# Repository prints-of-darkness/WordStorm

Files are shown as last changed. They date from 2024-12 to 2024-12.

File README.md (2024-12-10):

# Thermal Typewriter Project

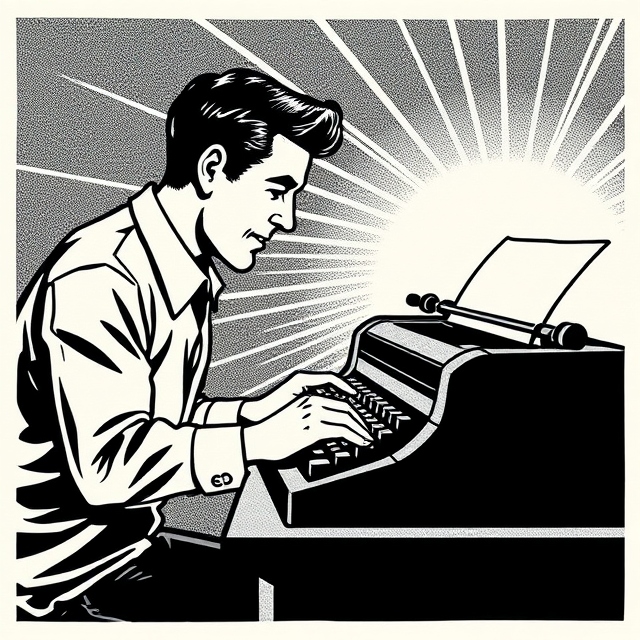
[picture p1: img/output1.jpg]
typewriter


 # Online BOM
 
 [BOM - WordStorm Cable Assy](https://www.digikey.com/en/mylists/list/2O8VW37YGK)
 
 [BOM - WordStorm R1.0](https://www.digikey.com/en/mylists/list/FTYAIGX1OS)
 
 [BOM - WordStorm Button](https://www.digikey.com/en/mylists/list/06NHDMXKI4)
 
 [BOM - WordStorm Debugger](https://www.digikey.com/en/mylists/list/TRGR0LOKP3)
 
 # Project Links

[Case](https://github.com/prints-of-darkness/WordStorm-Case)

[Display Module](https://github.com/prints-of-darkness/WordStorm-Display)

[Code](https://github.com/prints-of-darkness/WordStorm-Code)

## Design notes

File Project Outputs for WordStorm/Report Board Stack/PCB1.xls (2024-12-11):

Board Stack Report
Stack Up |  | Layer Stack
Layer | Board Layer Stack | Name | Material | Thickness | Constant
1 |  | Top Overlay |  | 0mil
2 |  | Top Solder | Solder Resist | 0.5mil | 3.8
3 |  | Top Layer |  | 1.378mil
4 |  | Dielectric 1 | 2313 | 3.937mil | 4.05
5 |  | Mid Layer 1 |  | 0.689mil
6 |  | Core | FR-4 | 49.803mil | 4.5
7 |  | Mid Layer 2 |  | 0.689mil
8 |  | Dielectric 2 | 2313 | 3.937mil | 4.05
9 |  | Bottom Layer |  | 1.378mil
10 |  | Bottom Solder | Solder Resist | 0.5mil | 3.8
11 |  | Bottom Overlay |  | 0mil
 | Height : 62.811mil

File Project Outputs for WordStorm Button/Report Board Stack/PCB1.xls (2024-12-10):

Board Stack Report
Stack Up |  | Layer Stack
Layer | Board Layer Stack | Name | Material | Thickness | Constant
1 |  | Top Overlay |  | 0mil
2 |  | Top Solder | Solder Resist | 0.5mil | 3.8
3 |  | Top Layer |  | 1.378mil
4 |  | Dielectric | FR-4 | 59.055mil | 4.5
5 |  | Bottom Layer |  | 1.378mil
6 |  | Bottom Solder | Solder Resist | 0.5mil | 3.8
7 |  | Bottom Overlay |  | 0mil
 | Height : 62.811mil

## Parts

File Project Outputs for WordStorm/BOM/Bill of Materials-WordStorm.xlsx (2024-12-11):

Line # | Name | Description | Designator | Quantity
 | CEM-1203(42) | Buzzers Transducer, Externally Driven Magnetic 3.5 V 35mA 2.048kHz 85dB @ 3.5V, 10cm Through Hole PC Pins | BUZZ1 | 1
 | GRM188R72A104MA35J | 0.1 µF ±20% 100V Ceramic Capacitor X7R 0603 (1608 Metric) | C1, C4, C7, C9, C16, C17, C18, C19, C20, C36, C37, C38, C39, C40, C41, C43, C45, C48, C49, C50, C51, C52, C53 | 23
 | C2012X5R1V226M125AC | CAP CER 22UF 35V X5R 0805 | C2, C5, C6, C8, C10, C11 | 6
 | GRM188R6YA106MA73D | 10 µF ±20% 35V Ceramic Capacitor X5R 0603 (1608 Metric) | C3, C13 | 2
 | GRM1885C2A471JA01D | 470 pF ±5% 100V Ceramic Capacitor C0G, NP0 0603 (1608 Metric) | C12 | 1
 | GRM188R6YA475KE15D | 4.7 µF ±10% 35V Ceramic Capacitor X5R 0603 (1608 Metric) | C14 | 1
 | GRM188R72A223KAC4D | 0.022 µF ±10% 100V Ceramic Capacitor X7R 0603 (1608 Metric) | C15, C31 | 2
 | EEE-FTH101XAP | CAP ALUM 100UF 20% 50V SMD | C21, C32 | 2
 | GRM188R72A103KA01D | 0.01 µF ±10% 100V Ceramic Capacitor X7R 0603 (1608 Metric) | C28, C29, C33, C34 | 4
 | GRM188R71H224KAC4D | 0.22 µF ±10% 50V Ceramic Capacitor X7R 0603 (1608 Metric) | C30 | 1
 | GRM188R7YA474KE05D | 0.47 µF ±10% 35V Ceramic Capacitor X7R 0603 (1608 Metric) | C35 | 1
 | GRM188D71H105KE01J | 1 µF ±10% 50V Ceramic Capacitor X7T 0603 (1608 Metric) | C42, C44 | 2
 | GRM188R61E225KA12J | 2.2 µF ±10% 25V Ceramic Capacitor X5R 0603 (1608 Metric) | C46, C47 | 2
 | ESD9X3.3ST5G | 10.4V Clamp 9.8A (8/20µs) Ipp Tvs Diode Surface Mount SOD-923 | D1, D2 | 2
 | FDLL4148 | Diode 100 V 200mA Surface Mount SOD-80 | D3 | 1
 | 3413.0326.22 | 7 A 32 V AC 63 V DC Fuse Board Mount (Cartridge Style Excluded) Surface Mount 1206 (3216 Metric) | F1 | 1
 | MPZ1608S221ATA00 | 220 Ohms @ 100 MHz 1 Power Line Ferrite Bead 0603 (1608 Metric) 2.2A 50mOhm | FB1 | 1
 | 54-00128 | Power Barrel Connector Jack 2.50mm ID (0.098"), 5.50mm OD (0.217") Through Hole, Right Angle | J1 | 1
 | 0530470210 | Connector Header Through Hole 2 position 0.049" (1.25mm) | J2 | 1
 | 10033527-N3112MLF | USB - mini AB USB 2.0 Receptacle Connector 5 Position Surface Mount, Right Angle | J3 | 1
 | 292303-1 | USB-A (USB TYPE-A) USB 2.0 Receptacle Connector 4 Position Through Hole, Right Angle | J4 | 1
 | B34B-PHDSS | Connector Header Through Hole 34 position 0.079" (2.00mm) | J5 | 1
 | 0530470410 | Connector Header Through Hole 4 position 0.049" (1.25mm) | J6 | 1
 | SFV16R-1STBE1HLF | 16 Position FFC, FPC Connector Contacts, Bottom 0.020" (0.50mm) Surface Mount, Right Angle | J7 | 1
 | 1255AY-3R9N=P3 | 3.9 µH Shielded Drum Core, Wirewound Inductor 4.2 A 22mOhm Nonstandard | L1 | 1
 | 744314650 | 6.5 µH Shielded Wirewound Inductor 6 A 21.5mOhm Nonstandard | L2 | 1
 | SISS65DN-T1-GE3 | P-Channel 30 V 25.9A (Ta), 94A (Tc) 5.1W (Ta), 65.8W (Tc) Surface Mount PowerPAK® 1212-8S | Q1 | 1
 | MMBT2222A-7-F | Bipolar (BJT) Transistor NPN 40 V 600 mA 300MHz 310 mW Surface Mount SOT-23-3 | Q2, Q3 | 2
 | RMCF0603FG10K0 | 10 kOhms ±1% 0.1W, 1/10W Chip Resistor 0603 (1608 Metric) Automotive AEC-Q200 Thick Film | R1, R8, R11, R12, R15, R17, R22, R23, R24, R25, R26, R27, R28, R29, R30, R50, R52, R56 | 18
 | RMCF0603FG20K0 | 20 kOhms ±1% 0.1W, 1/10W Chip Resistor 0603 (1608 Metric) Automotive AEC-Q200 Thick Film | R2, R7 | 2
 | RMCF0603FT180R | 180 Ohms ±1% 0.1W, 1/10W Chip Resistor 0603 (1608 Metric) Automotive AEC-Q200 Thick Film | R3, R48 | 2
 | RMCF0603FG100K | 100 kOhms ±1% 0.1W, 1/10W Chip Resistor 0603 (1608 Metric) Automotive AEC-Q200 Thick Film | R4, R5, R6, R14, R16, R31, R33, R37, R49 | 9
 | RMCF0603FT360K | 360 kOhms ±1% 0.1W, 1/10W Chip Resistor 0603 (1608 Metric) Automotive AEC-Q200 Thick Film | R9 | 1
 | RMCF0603FT40K2 | 40.2 kOhms ±1% 0.1W, 1/10W Chip Resistor 0603 (1608 Metric) Automotive AEC-Q200 Thick Film | R10 | 1
 | RMCF0603FG1K00 | 1 kOhms ±1% 0.1W, 1/10W Chip Resistor 0603 (1608 Metric) Automotive AEC-Q200 Thick Film | R13, R19 | 2
 | YC164-JR-07100RL | 100 Ohm ±5% 62.5mW Power Per Element Isolated 4 Resistor Network/Array ±200ppm/°C 1206 (3216 Metric), Convex, Long Side Terminals | R18, R20, R21, R53, R54, R55 | 6
 | RMCF0603FG15K0 | 15 kOhms ±1% 0.1W, 1/10W Chip Resistor 0603 (1608 Metric) Automotive AEC-Q200 Thick Film | R32, R40, R42, R44, R46 | 5
 | RMCF0603FT48K7 | 48.7 kOhms ±1% 0.1W, 1/10W Chip Resistor 0603 (1608 Metric) Automotive AEC-Q200 Thick Film | R34 | 1
 | RMCF0603FT80K6 | 80.6 kOhms ±1% 0.1W, 1/10W Chip Resistor 0603 (1608 Metric) Automotive AEC-Q200 Thick Film | R35 | 1
 | RMCF0603FG16K0 | 16 kOhms ±1% 0.1W, 1/10W Chip Resistor 0603 (1608 Metric) Automotive AEC-Q200 Thick Film | R36 | 1
 | RMCF0603FT63K4 | 63.4 kOhms ±1% 0.1W, 1/10W Chip Resistor 0603 (1608 Metric) Automotive AEC-Q200 Thick Film | R38 | 1
 | RMCF0603FG39K0 | 39 kOhms ±1% 0.1W, 1/10W Chip Resistor 0603 (1608 Metric) Automotive AEC-Q200 Thick Film | R39 | 1
 | RMCF0603FG100R | 100 Ohms ±1% 0.1W, 1/10W Chip Resistor 0603 (1608 Metric) Automotive AEC-Q200 Thick Film | R41, R45 | 2
 | RMCF0603FG24K0 | 24 kOhms ±1% 0.1W, 1/10W Chip Resistor 0603 (1608 Metric) Automotive AEC-Q200 Thick Film | R43, R47 | 2
 | RMCF0603ZT0R00 | 0 Ohms Jumper Chip Resistor 0603 (1608 Metric) Automotive AEC-Q200 Thick Film | R51 | 1
 | 1040310811 | 10 (8 + 2) Position Card Connector Secure Digital - microSD™ Surface Mount, Right Angle Gold | SD1 | 1
 | AP63203WU-7 | Buck Switching Regulator IC Positive Fixed 3.3V 1 Output 2A SOT-23-6 Thin, TSOT-23-6 | U1 | 1
 | TPS7B6933QDCYRQ1 | Linear Voltage Regulator IC Positive Fixed 1 Output 150mA SOT-223-4 | U2 | 1
 | MP2338GTL-Z | Buck Switching Regulator IC Positive Adjustable 0.5V 1 Output 3A SOT-583 | U3 | 1
 | ATTINY85-20PU | AVR AVR® ATtiny, Functional Safety (FuSa) Microcontroller IC 8-Bit 20MHz 8KB (4K x 16) FLASH 8-PDIP | U4 | 1
 | STMPS2141STR | Power Switch/Driver 1:1 N-Channel 500mA SOT-23-5 | U5 | 1
 | TS3USB221ARSER | USB Switch IC 2 Channel 10-UQFN (2.0x1.5) | U6 | 1
 | SN74LVC2G34DBVR | Buffer, Non-Inverting 2 Element 1 Bit per Element Push-Pull Output SOT-23-6 | U7 | 1
 | SN74LVC541APWR | Buffer, Non-Inverting 1 Element 8 Bit per Element 3-State Output 20-TSSOP | U8 | 1
 | DRV8426RGER | Bipolar Motor Driver Power MOSFET Step/Direction 24-VQFN (4x4) | U9 | 1
 | MCP6561T-E/LT | Comparator General Purpose CMOS, Push-Pull, Rail-to-Rail, TTL SC-70-5 | U10, U11, U12, U13 | 4
 | W25Q64JVSSIQ | FLASH - NOR Memory IC 64Mbit SPI - Quad I/O 133 MHz 8-SOIC | U14 | 1
 | STM32H743VIT6 | ARM® Cortex®-M7 STM32H7 Microcontroller IC 32-Bit Single-Core 480MHz 2MB (2M x 8) FLASH 100-LQFP (14x14) | U15 | 1
 | APX809S-31SA-7 | Supervisor Push-Pull, Totem Pole 1 Channel SOT-23-3 | U16 | 1
 | CSTNE8M00G550000R0 | 8 MHz Ceramic Resonator Built in Capacitor 33 pF ±0.2% 40 Ohms -40°C ~ 85°C Surface Mount | X1 | 1

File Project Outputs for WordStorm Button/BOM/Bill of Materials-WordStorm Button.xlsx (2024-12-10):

Name | Description | Designator | Quantity
0530470210 | Connector Header Through Hole 2 position 0.049" (1.25mm) | J1 | 1
TS02-66-150-BK-100-LCR-D | Tactile Switch SPST-NO Top Actuated Through Hole | S1 | 1

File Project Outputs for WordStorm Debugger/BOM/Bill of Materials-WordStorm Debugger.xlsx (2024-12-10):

Name | Description | Designator | Quantity
SFH11-PBPC-D10-ST-BK | 20 Position Header Connector 0.100" (2.54mm) Through Hole Gold | J1 | 1
0530470410 | Connector Header Through Hole 4 position 0.049" (1.25mm) | J2 | 1

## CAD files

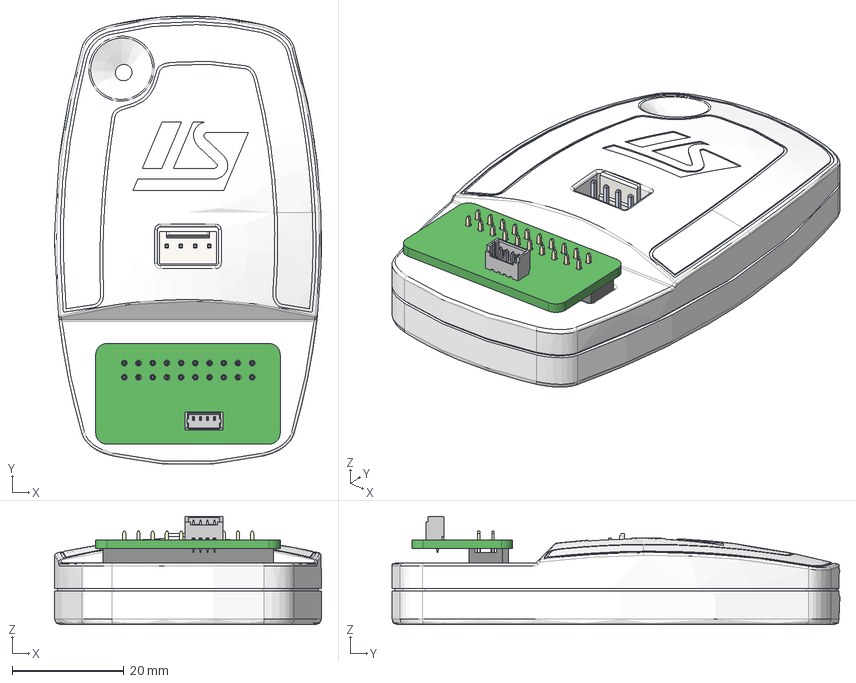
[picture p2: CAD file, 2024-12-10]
Debugger_Step/stlink_v2.step
47.7 x 80.1 x 19.4 mm
SFH11-xC-Dx-ST-BK body_10
pin^SFH11-xC-Dx-ST-BK Ass x 20
PinHeader_2x10_P254mm_Vertical
USB_Mini-B_Lumberg_2486_01_Horizontal
WF_(DS1070_CONNFLY)

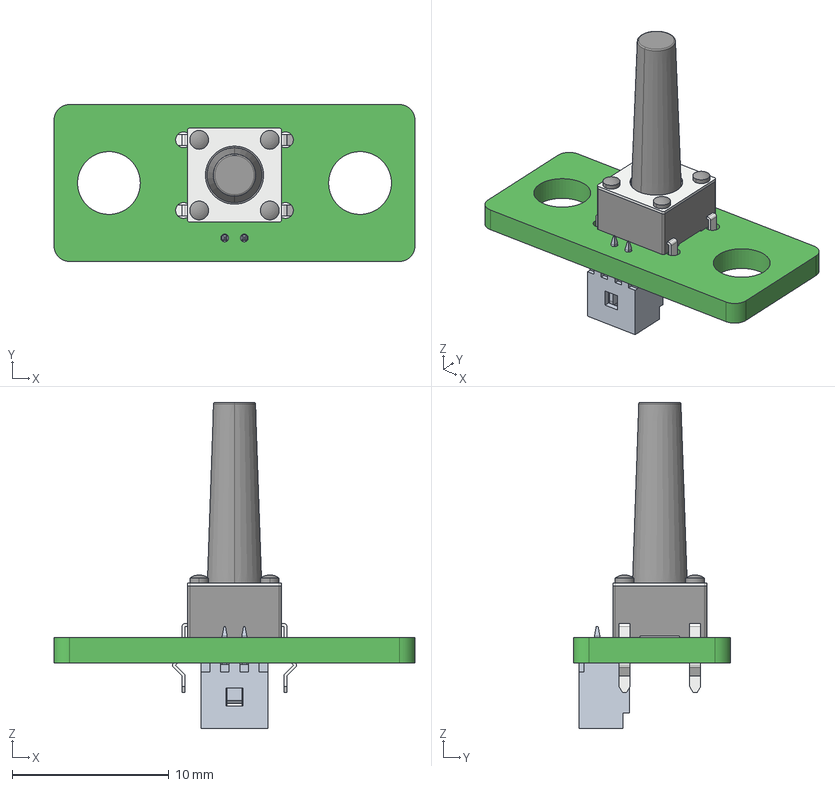
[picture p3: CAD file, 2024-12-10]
Project Outputs for WordStorm Button/ExportSTEP/PCB1.step
23.0 x 10.0 x 20.8 mm
Same_Sky_TS02-66-150-BK-100-LCR-D

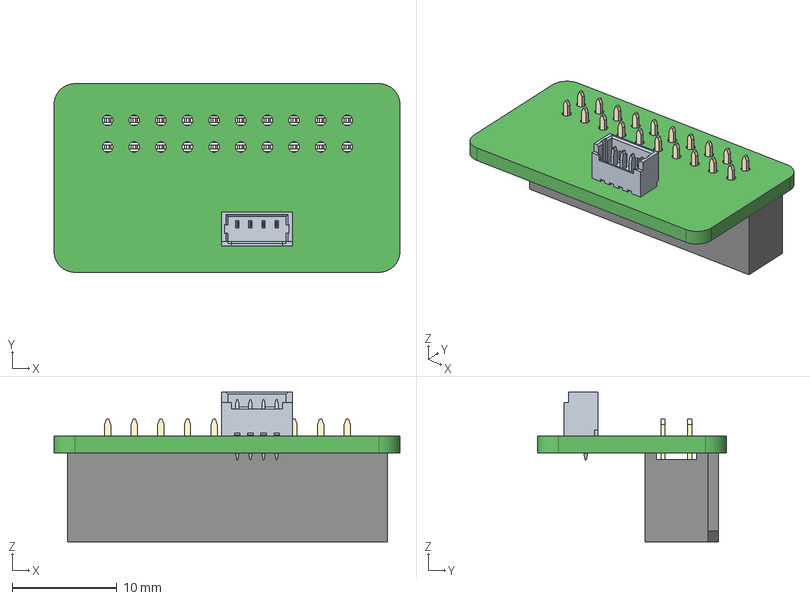
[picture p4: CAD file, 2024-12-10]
Project Outputs for WordStorm Debugger/ExportSTEP/PCB1.step
33.0 x 18.0 x 14.3 mm
SFH11-xC-Dx-ST-BK body_10
pin^SFH11-xC-Dx-ST-BK Ass x 20

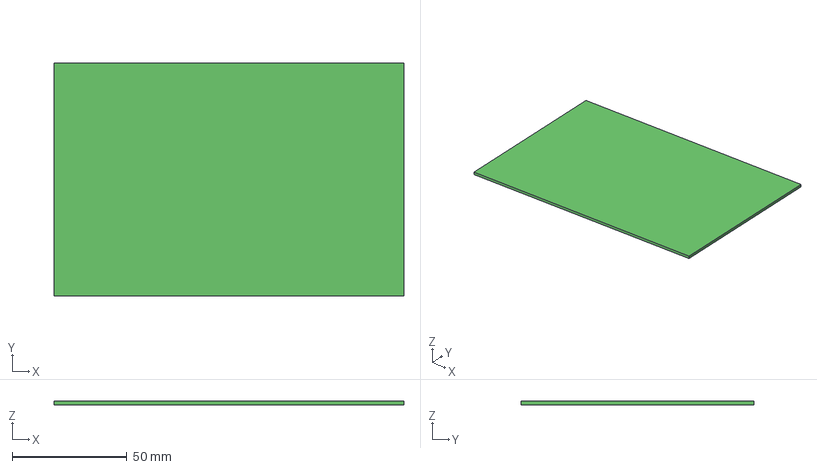
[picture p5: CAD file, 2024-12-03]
Project Outputs for WordStorm/ExportSTEP/PCB1.step
152.4 x 101.6 x 1.60 mm

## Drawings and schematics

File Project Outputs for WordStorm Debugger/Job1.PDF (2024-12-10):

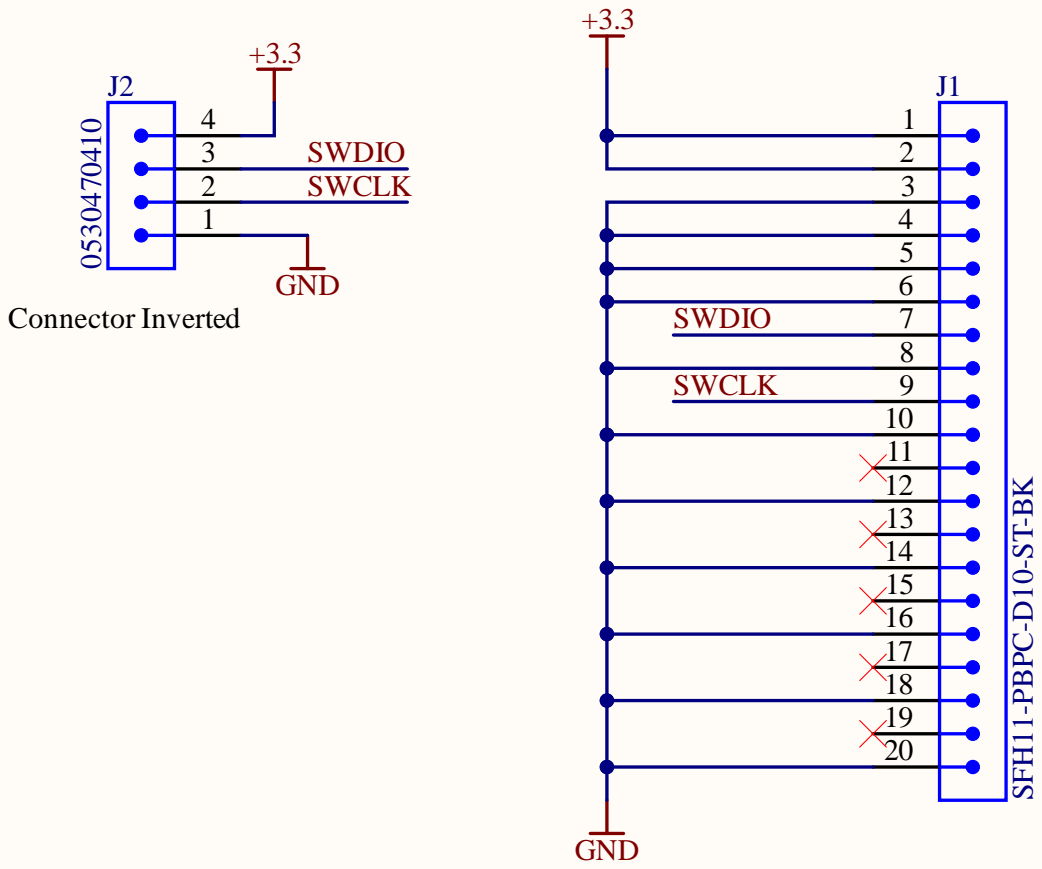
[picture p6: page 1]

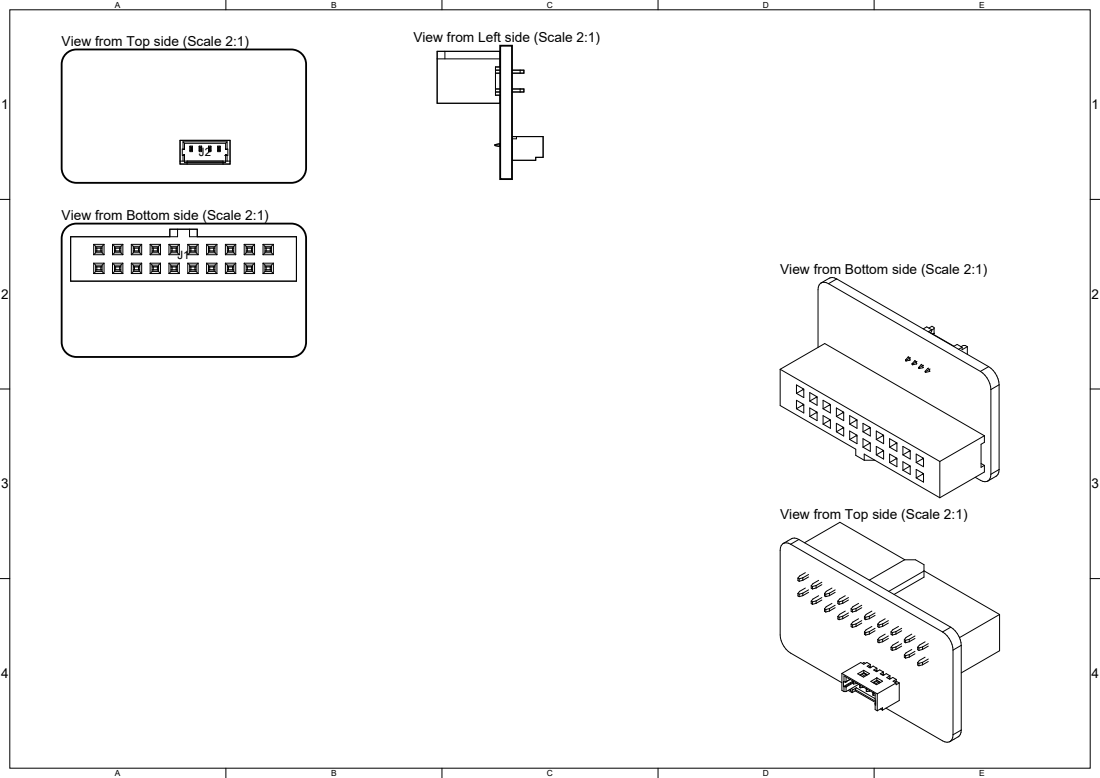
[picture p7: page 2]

View from Top side (Scale 2:1)

View from Left side (Scale 2:1)

View from Bottom side (Scale 2:1)

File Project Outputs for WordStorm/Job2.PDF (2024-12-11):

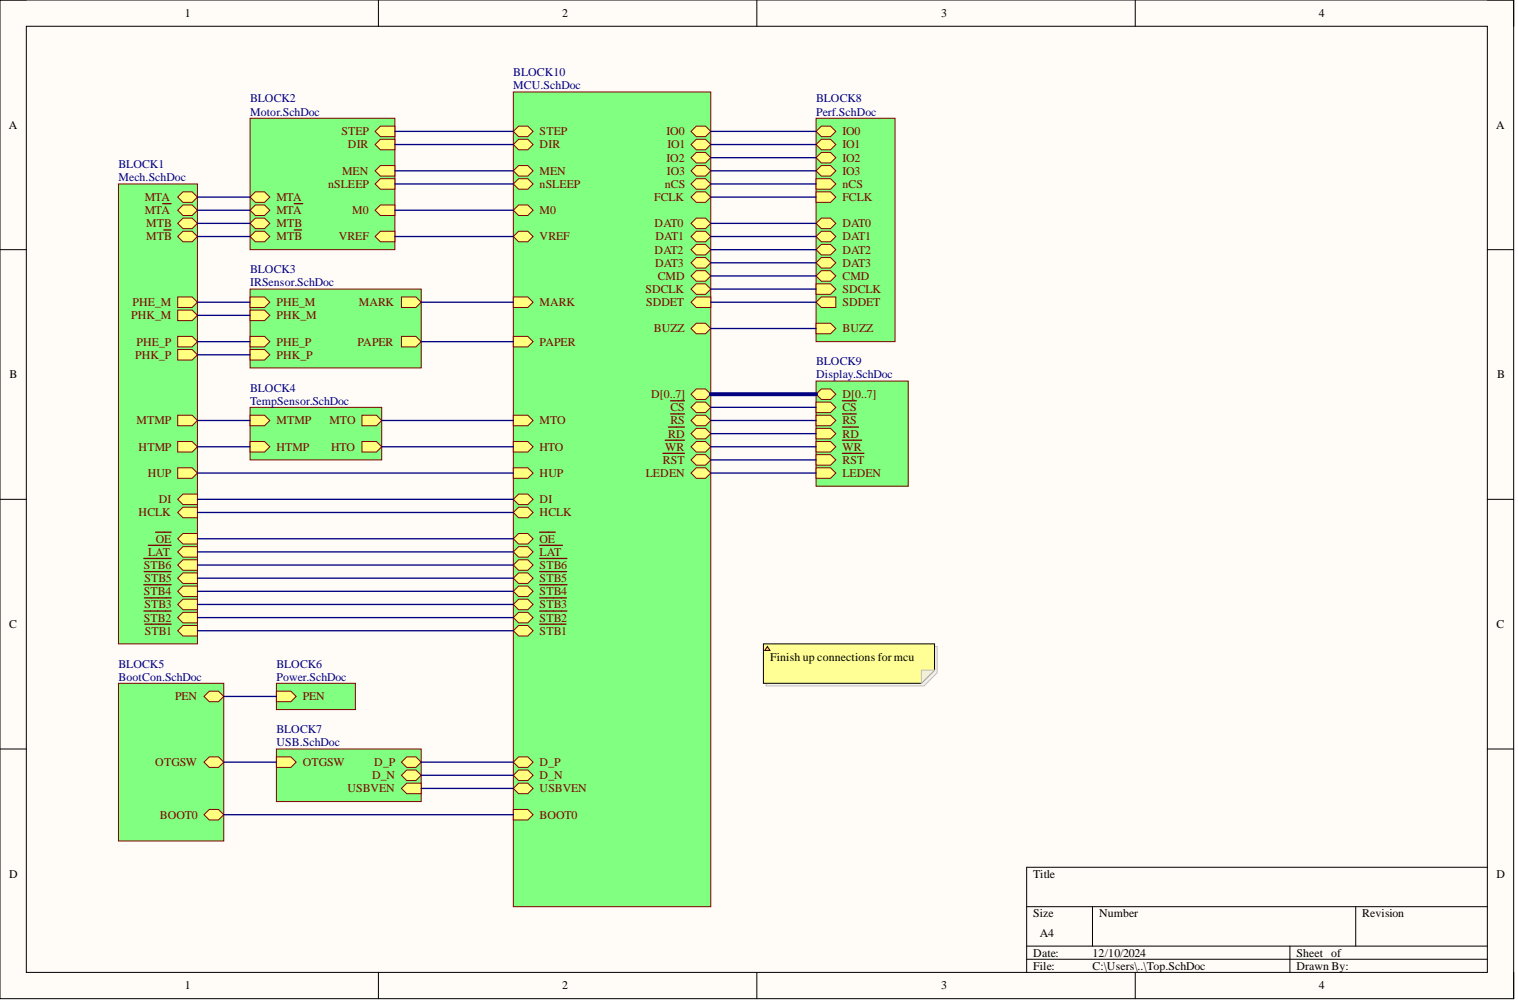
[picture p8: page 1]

Finish up connections for mcu

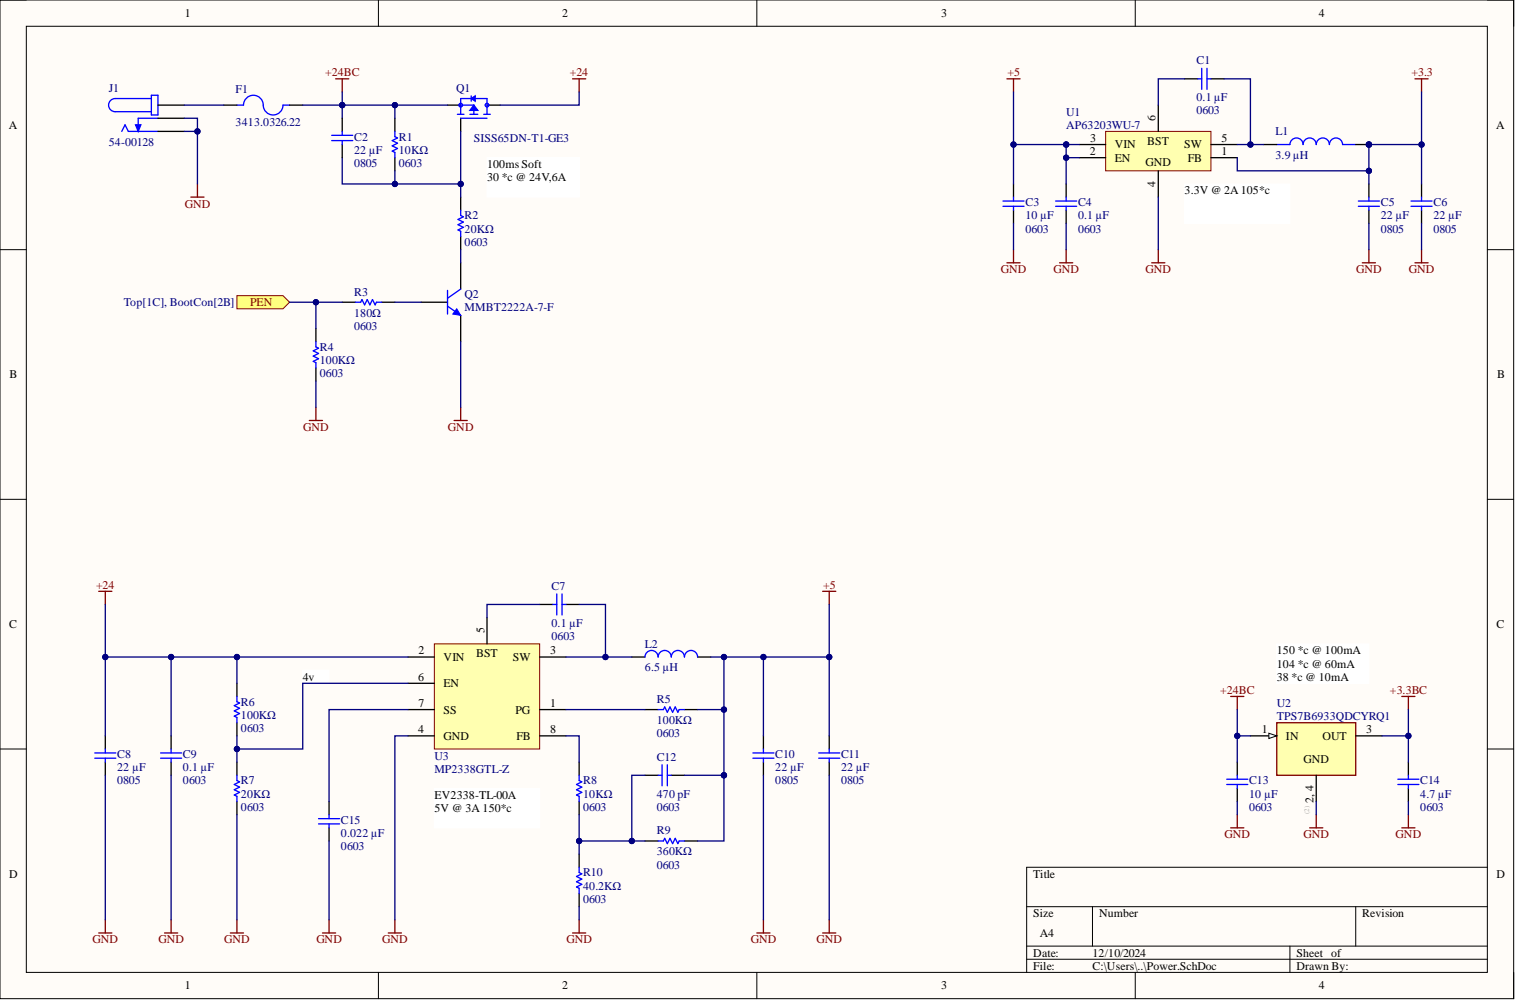
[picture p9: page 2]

GND 4

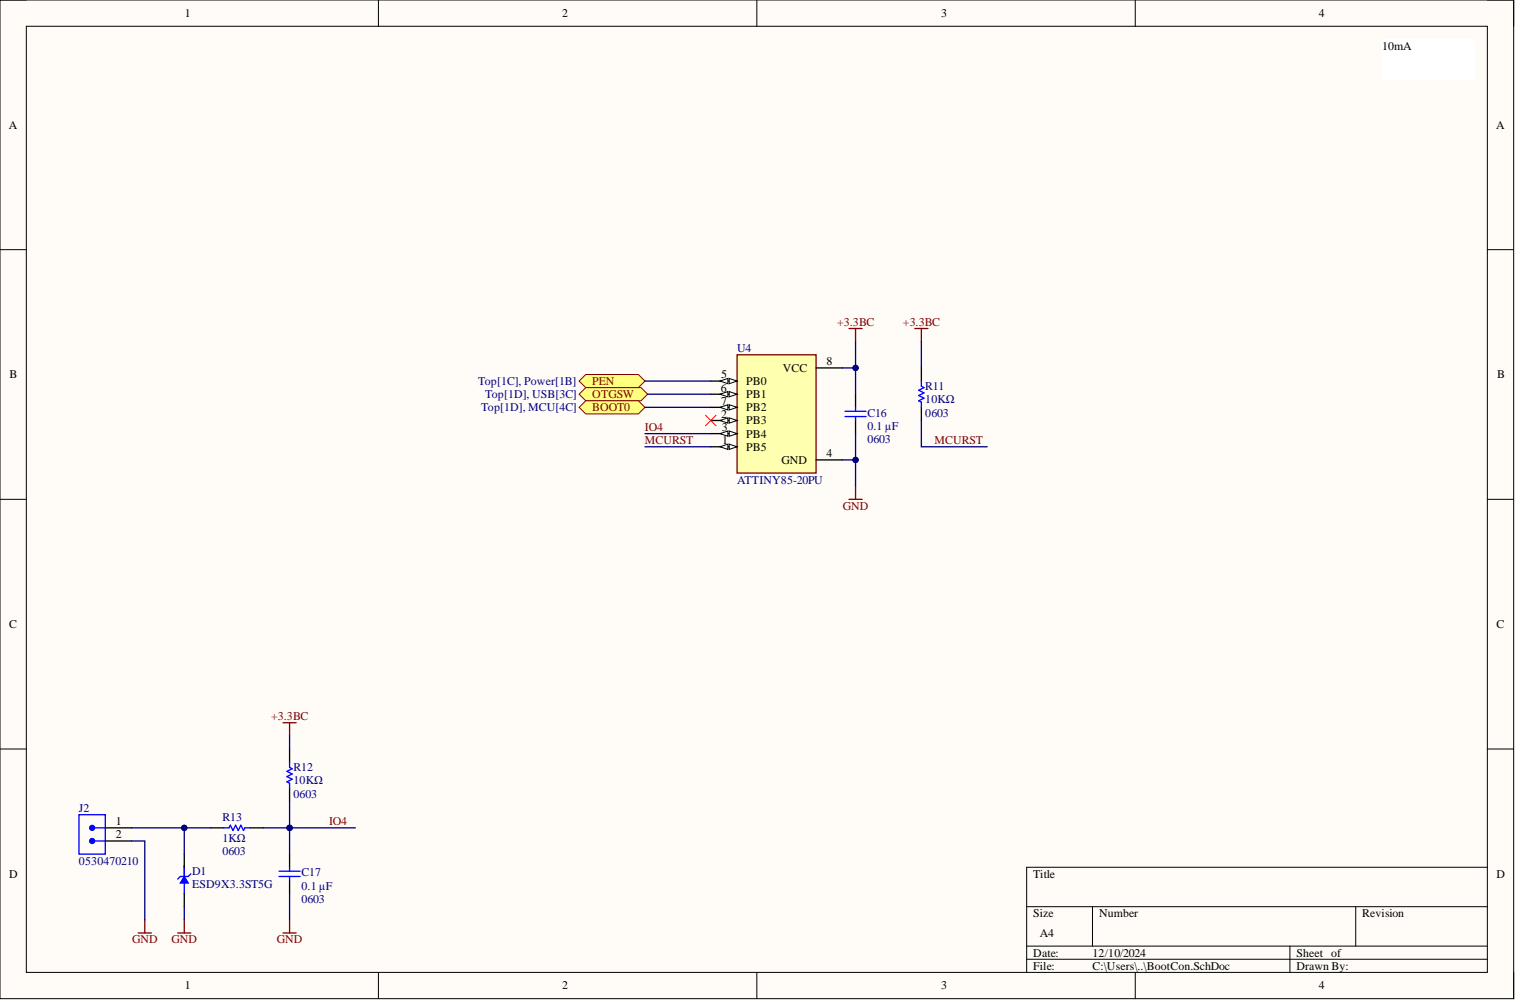
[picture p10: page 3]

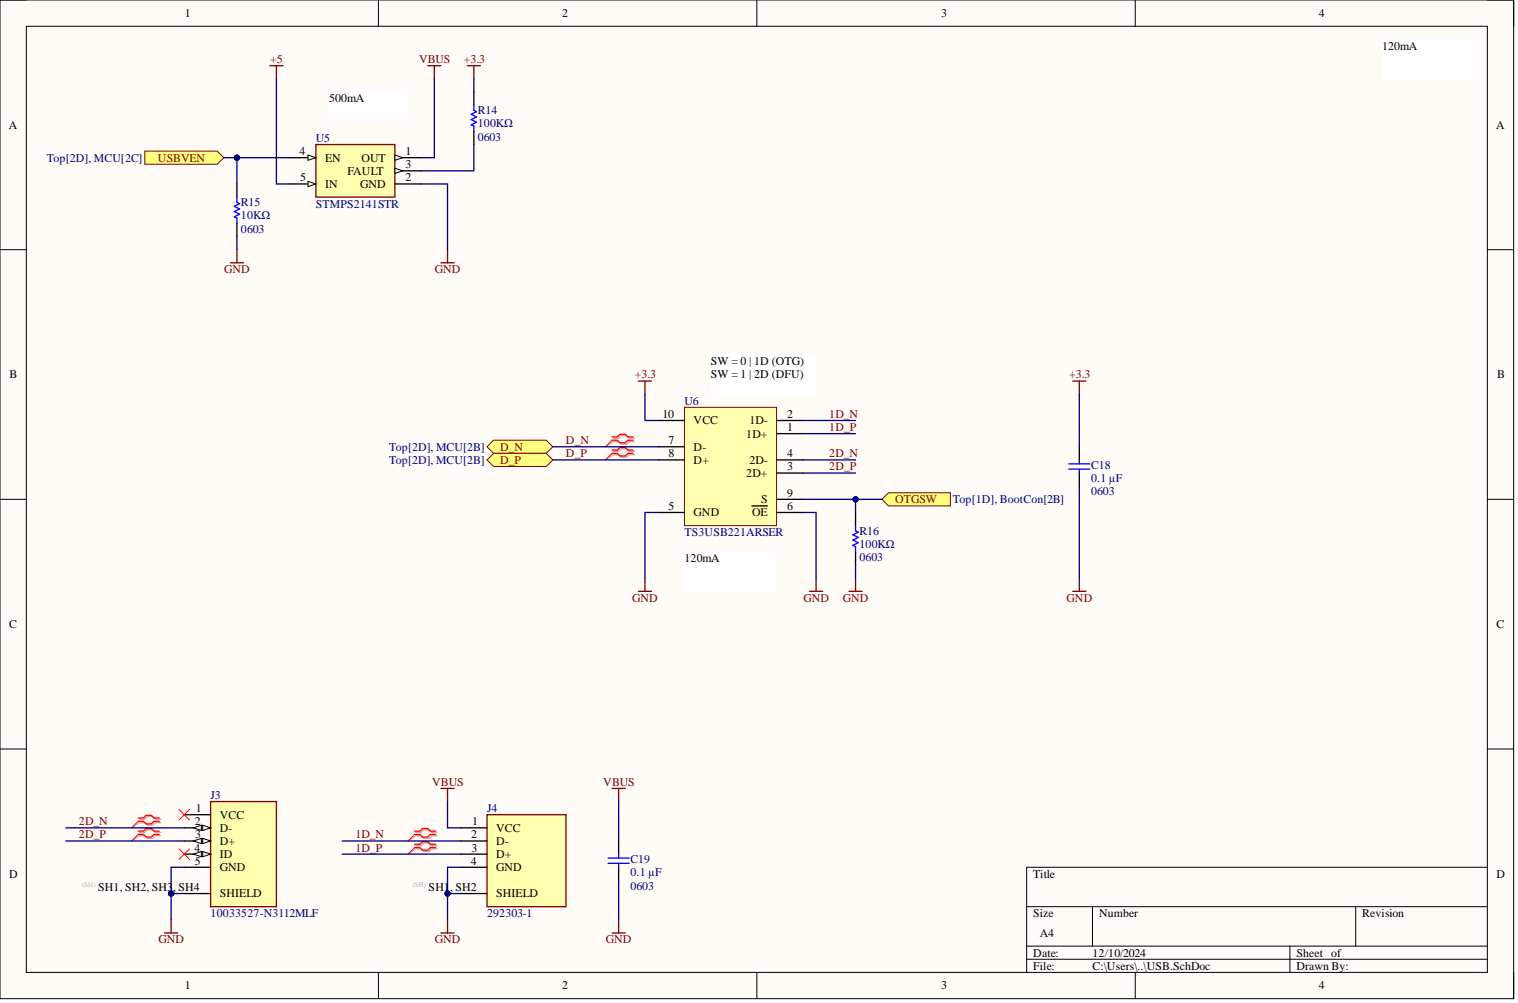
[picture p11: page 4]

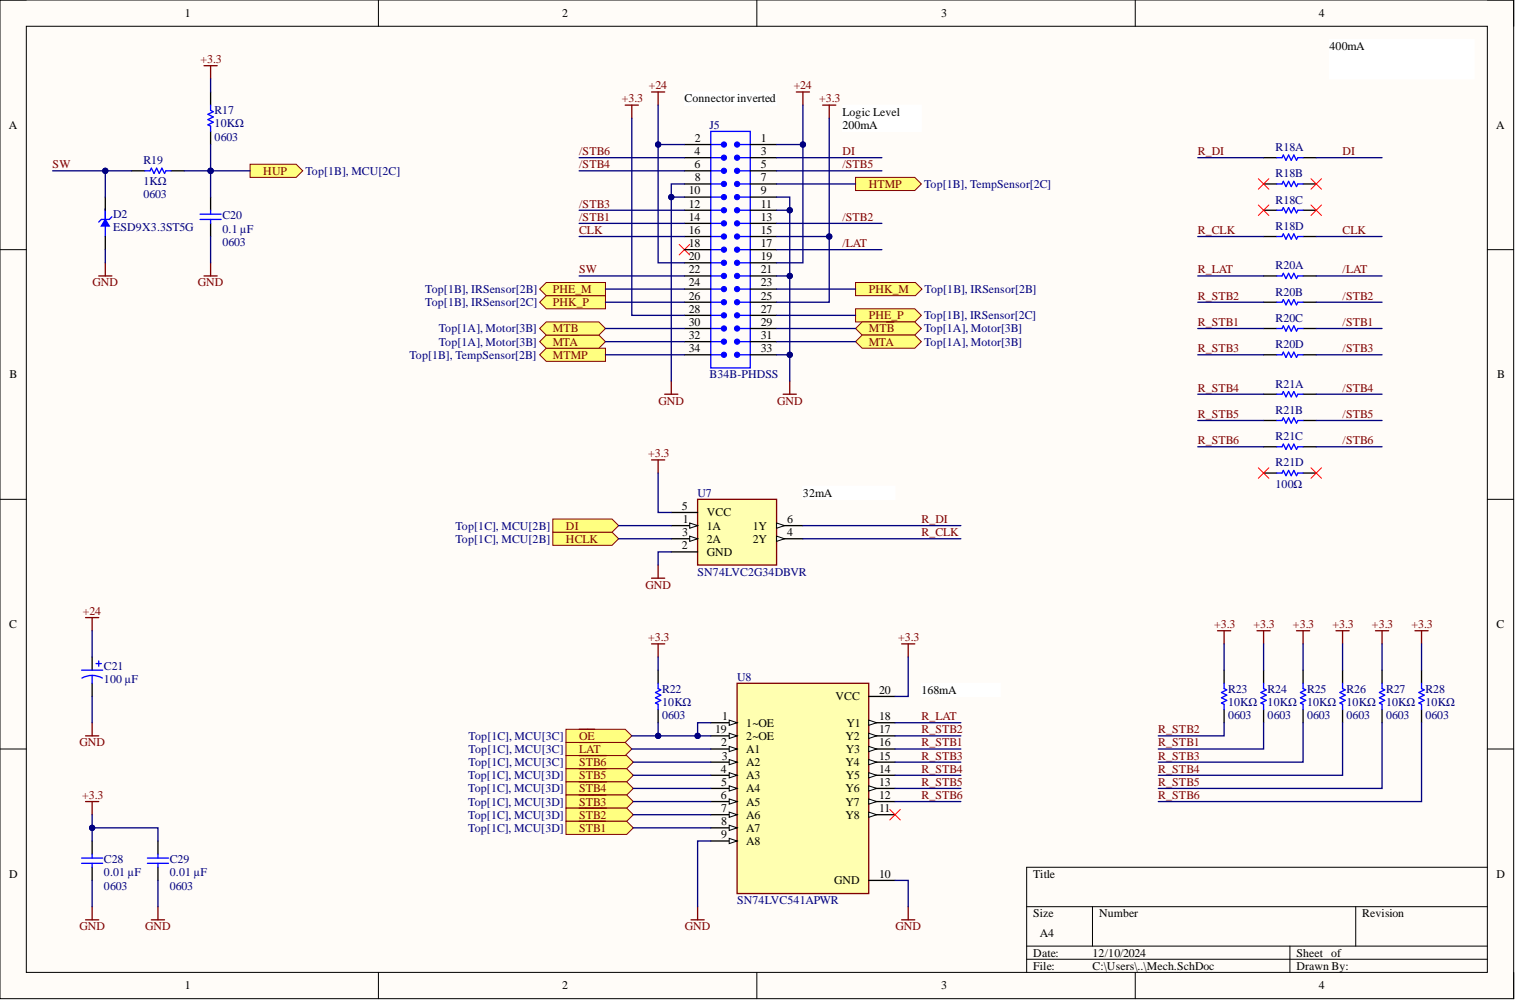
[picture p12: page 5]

1 1
1 3 1 5

2 1
2 3 2 5

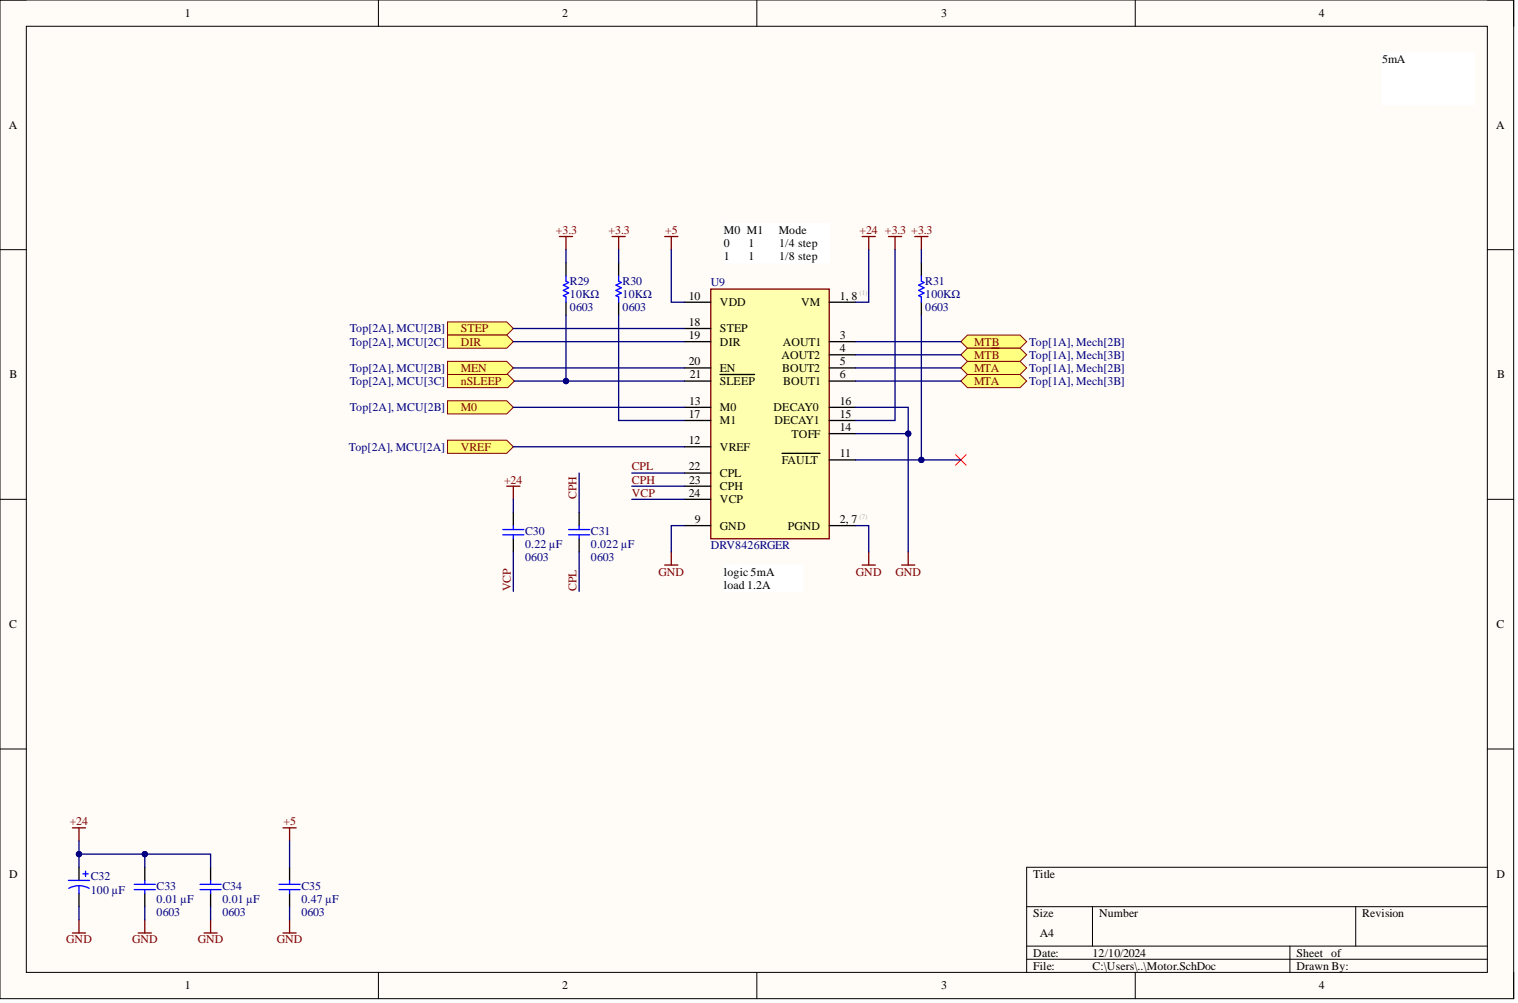
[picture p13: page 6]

DIR 19

EN 20
SLEEP 21

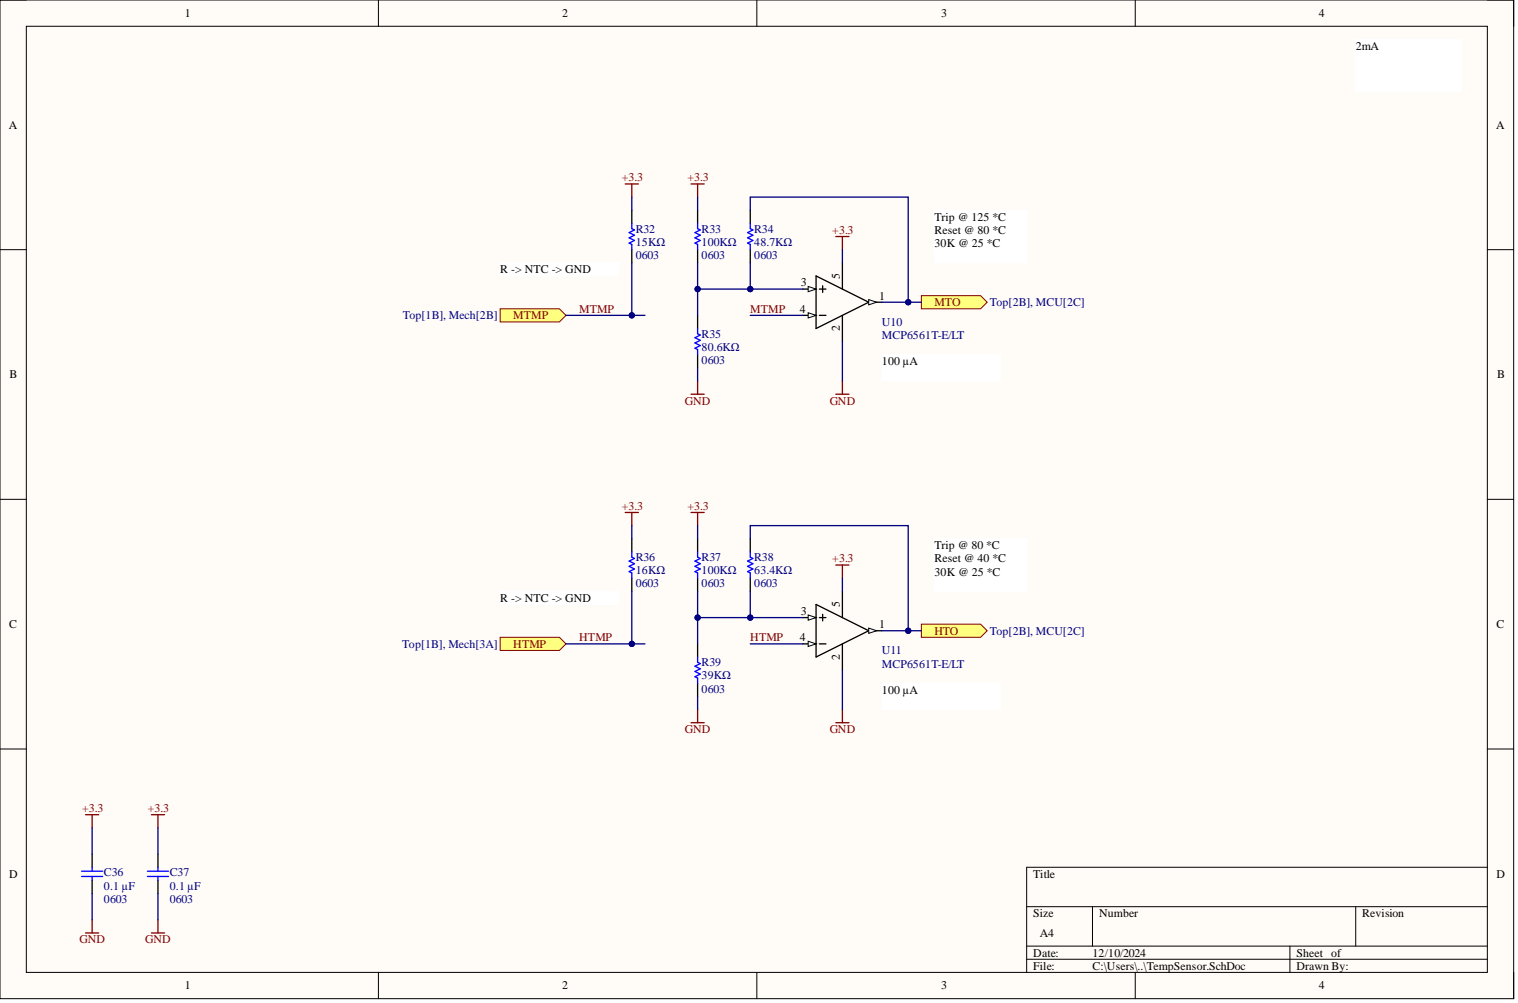
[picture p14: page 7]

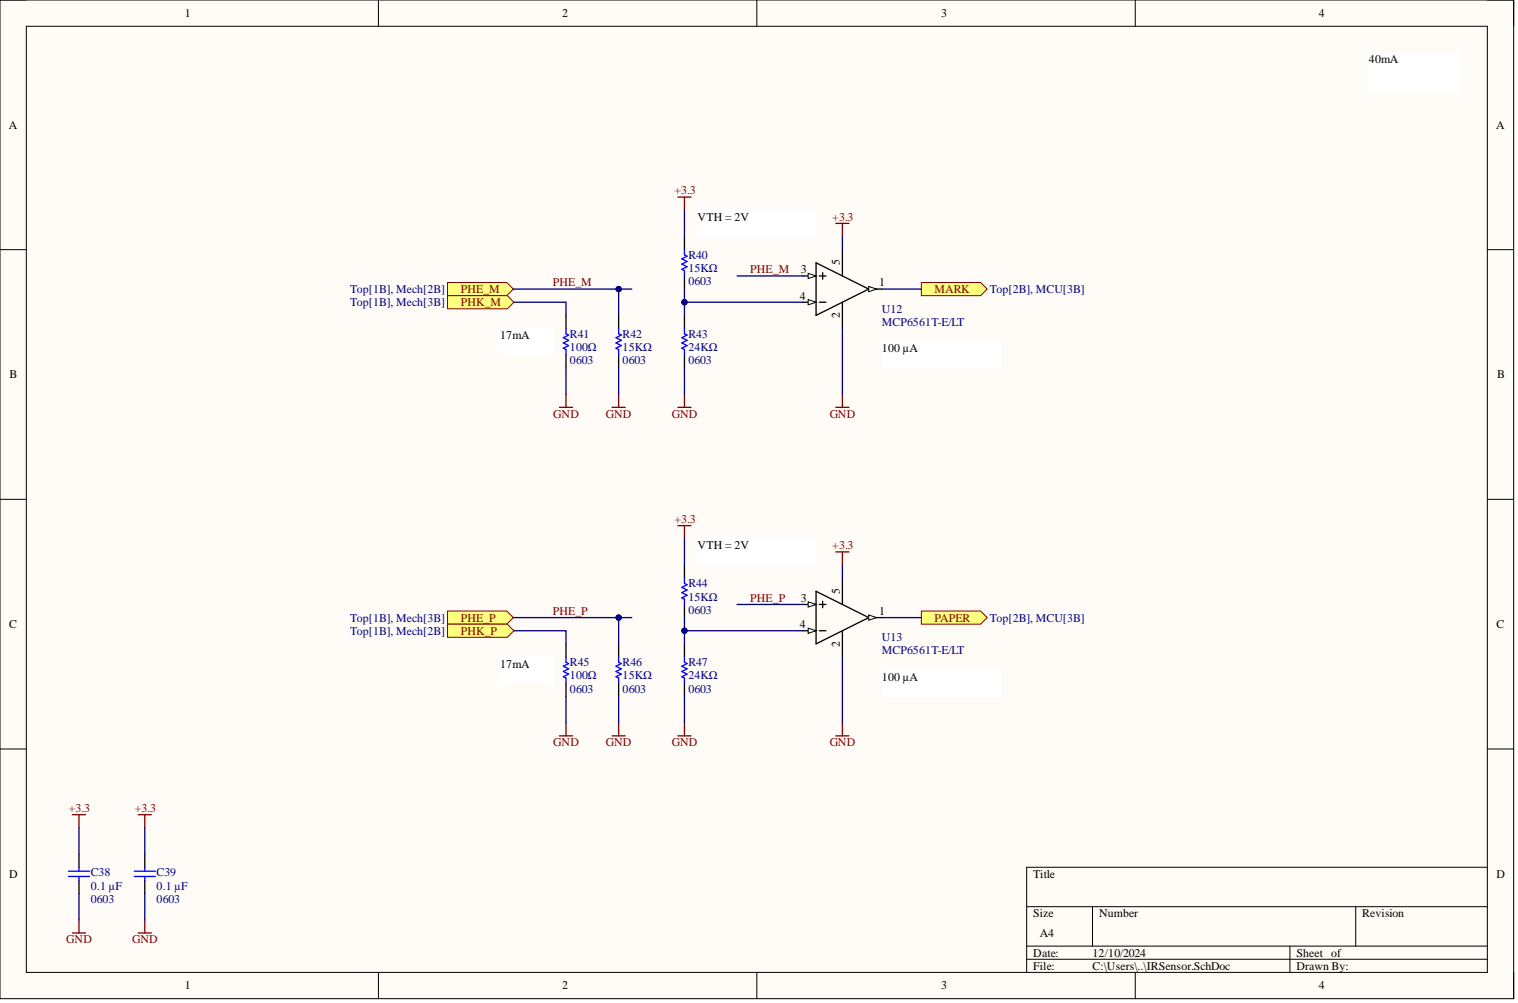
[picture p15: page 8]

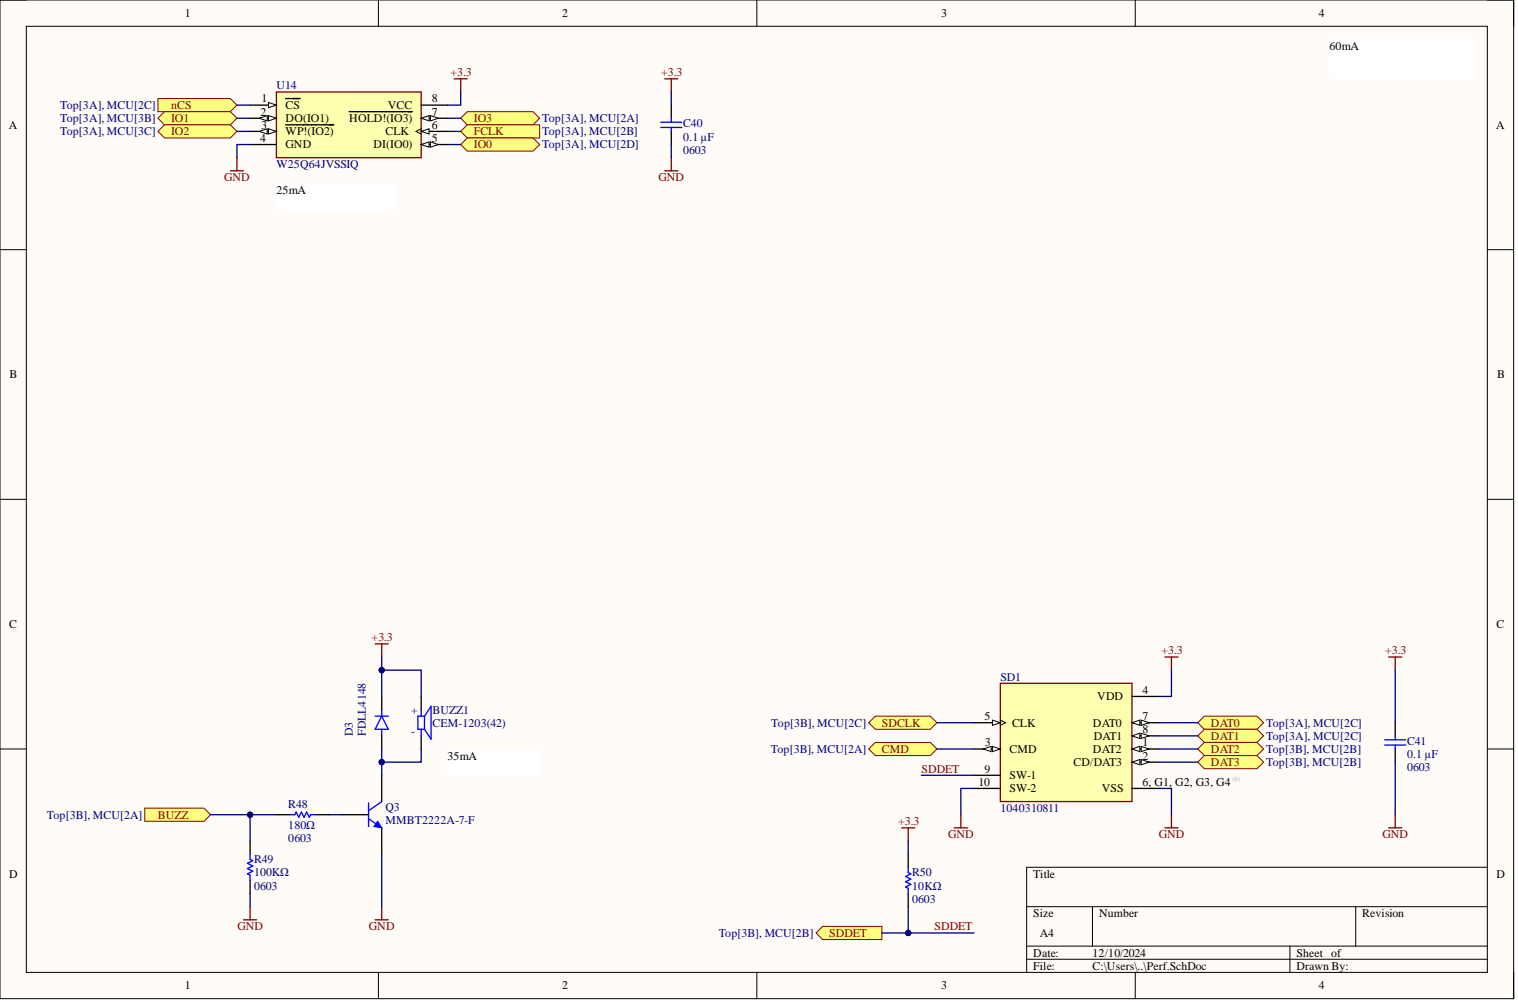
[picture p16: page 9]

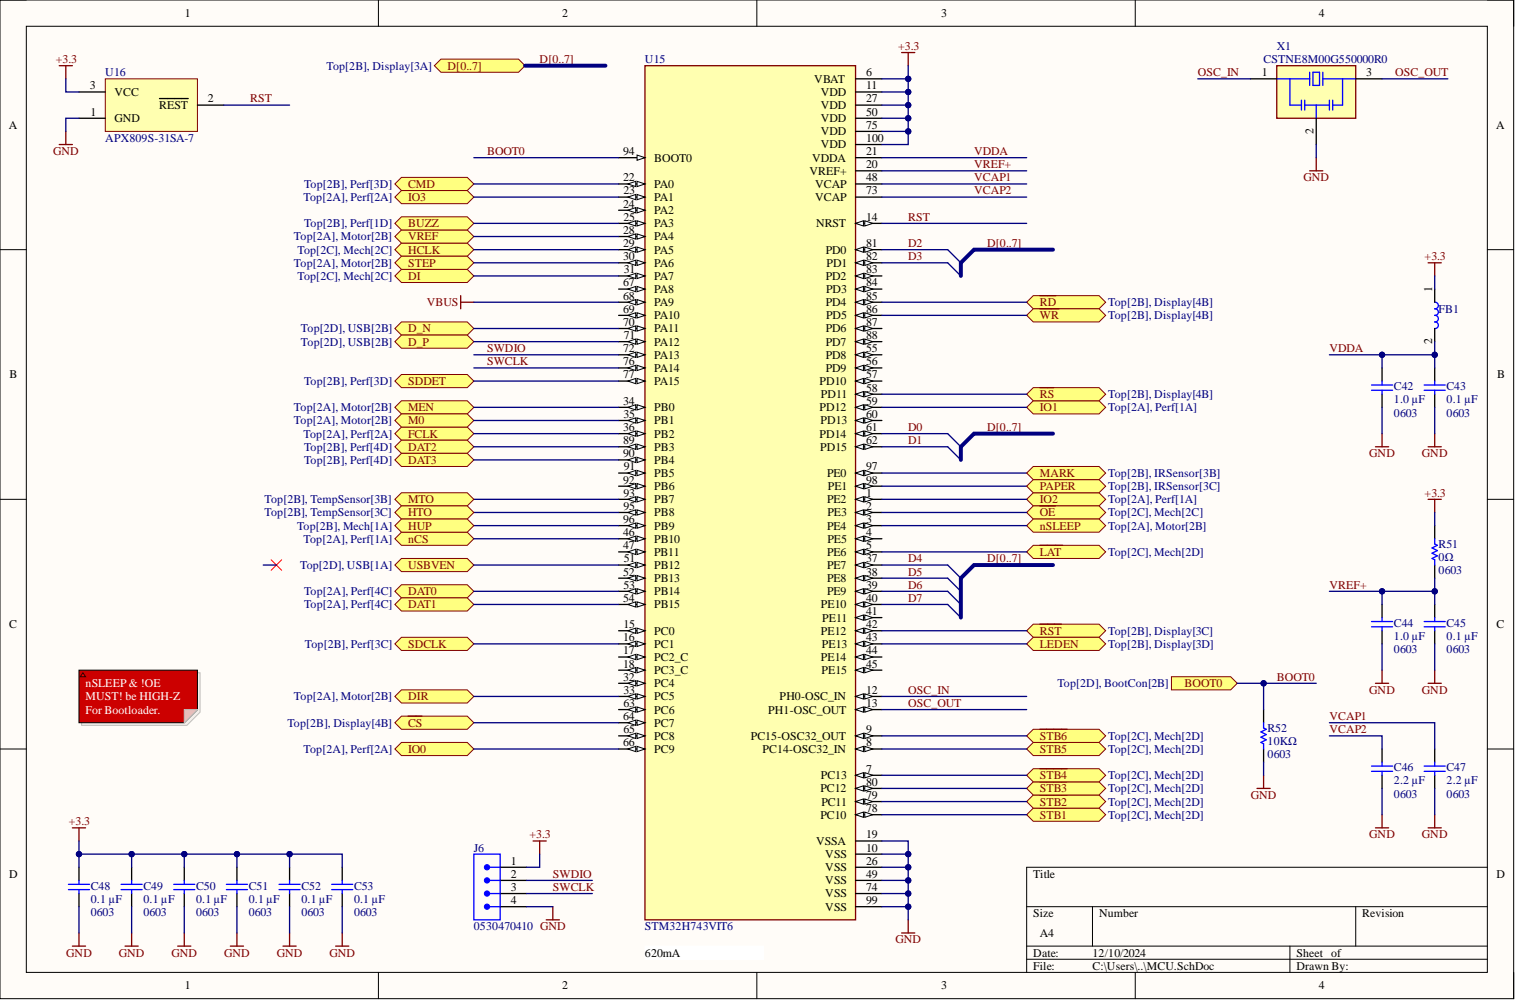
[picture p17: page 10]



View from Top side (Scale 2:1)



View from Top side (Scale 1:1)

View from Left side (Scale 1:1)

View from Bottom side (Scale 1:1)

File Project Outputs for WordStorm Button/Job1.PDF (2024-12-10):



View from Top side (Scale 2:1)

View from Left side (Scale 2:1)

View from Bottom side (Scale 2:1)

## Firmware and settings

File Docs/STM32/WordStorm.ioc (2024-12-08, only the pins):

Mcu.UserName=STM32H743VITx
PA0.Signal=SDMMC2_CMD
PA1.Signal=QUADSPI_BK1_IO3
PA11.Signal=USB_OTG_FS_DM
PA12.Signal=USB_OTG_FS_DP
PA3.GPIO_Label=BUZZ
PA3.Signal=GPIO_Output
PA4.Signal=COMP_DAC11_group
PA5.Signal=SPI1_SCK
PA6.GPIO_Label=STEP
PA6.Signal=GPIO_Output
PA7.Signal=SPI1_MOSI
PA9.Signal=USB_OTG_FS_VBUS
PB0.GPIO_Label=MEN
PB0.Signal=GPIO_Output
PB1.GPIO_Label=M0
PB1.Signal=GPIO_Output
PB10.Signal=QUADSPI_BK1_NCS
PB12.GPIO_Label=USBEN
PB12.Signal=GPIO_Output
PB14.Signal=SDMMC2_D0
PB15.Signal=SDMMC2_D1
PB2.Signal=QUADSPI_CLK
PB7.GPIO_Label=MTO
PB7.Signal=GPIO_Input
PB8.GPIO_Label=HTO
PB8.Signal=GPIO_Input
PB9.GPIO_Label=HUP
PB9.Signal=GPIO_Input
PC1.Signal=SDMMC2_CK
PC10.GPIO_Label=STB1
PC10.Signal=GPIO_Output
PC11.GPIO_Label=STB2
PC11.Signal=GPIO_Output
PC12.GPIO_Label=STB3
PC12.Signal=GPIO_Output
PC13.GPIO_Label=STB4
PC13.Signal=GPIO_Output
PC5.GPIO_Label=DIR
PC5.Signal=GPIO_Output
PC7.Signal=FMC_NE1
PC9.Signal=QUADSPI_BK1_IO0
PD0.Signal=FMC_D2_DA2
PD1.Signal=FMC_D3_DA3
PD11.Signal=FMC_A16_CLE
PD12.Signal=QUADSPI_BK1_IO1
PD14.Signal=FMC_D0_DA0
PD15.Signal=FMC_D1_DA1
PD4.Signal=FMC_NOE
PD5.Signal=FMC_NWE
PE0.GPIO_Label=MARK
PE0.Signal=GPIO_Input
PE1.GPIO_Label=PAPER
PE1.Signal=GPIO_Input
PE10.Signal=FMC_D7_DA7
PE12.GPIO_Label=RST
PE12.Signal=GPIO_Output
PE13.GPIO_Label=LEDEN
PE13.Signal=GPIO_Output
PE2.Signal=QUADSPI_BK1_IO2
PE3.GPIO_Label=nOE
PE3.Signal=GPIO_Output
PE4.GPIO_Label=nSLEEP
PE4.Signal=GPIO_Output
PE6.GPIO_Label=LAT
PE6.Signal=GPIO_Output
PE7.Signal=FMC_D4_DA4
PE8.Signal=FMC_D5_DA5
PE9.Signal=FMC_D6_DA6

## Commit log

2024-12-04 working on layout
    WIP, backed up to the hub.
    [Bill of Materials-WordStorm.xlsx, BootCon.SchDoc, Display.SchDoc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]
2024-12-04 more micro/group routing
    I'm done for the day. Notes to self: don't get burnt out.
    [Bill of Materials-WordStorm.xlsx, BootCon.SchDoc, Display.SchDoc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]
2024-12-04 redid power section
    power entry was too complicated, so I made it simple-er.
    [Bill of Materials-WordStorm.xlsx, BootCon.SchDoc, Display.SchDoc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]
2024-12-04 bumped soft start time to 100ms
    swapped 4.7uf for 22uf.
    [Bill of Materials-WordStorm.xlsx, BootCon.SchDoc, Display.SchDoc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]
2024-12-04 fixed display connector wires.
    [Bill of Materials-WordStorm.xlsx, BootCon.SchDoc, Display.SchDoc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]
2024-12-08 backup
    I may redo the layout, and I still need to route power.
    [Bill of Materials-WordStorm.xlsx, BootCon.SchDoc, Display.SchDoc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]
2024-12-09 added button PCB
    [Bill of Materials-WordStorm Button.xlsx, PCB1.PcbDoc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]
2024-12-09 fixed step export
    [Bill of Materials-WordStorm Button.xlsx, PCB1.PcbDoc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]
2024-12-09 added debugger pcb for quick connection of stlink/v2
    [Bill of Materials-WordStorm Debugger.xlsx, PCB1.PcbDoc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]
2024-12-09 added draftsman doc
    [Bill of Materials-WordStorm Debugger.xlsx, PCB1.PcbDoc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]
2024-12-10 re-exported all project files.
    [Bill of Materials-WordStorm Button.xlsx, Bill of Materials-WordStorm Debugger.xlsx, Bill of Materials-WordStorm.xlsx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]
2024-12-11 added another draftman file
    [Bill of Materials-WordStorm.xlsx, BootCon.SchDoc, Display.SchDoc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]
